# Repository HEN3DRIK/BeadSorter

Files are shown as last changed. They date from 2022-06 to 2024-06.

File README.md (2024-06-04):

- 👋 Hi, I’m @HEN3DRIK
- 👀 I’m interested in 3DPrinting and Electroforming/Electroplating
- 📫 How to reach me 
  - Youtube https://youtube.com/@hen3drik
  - Twitter https://twitter.com/hen3drik

# BeadSorter
Nice to have you here. In this repository I keep the files that are necessary for the BeadSorter. Also there will be documentation about the needed electronics and software. I will update this repo continuously.

# Video
perlerbead sorting machine (https://www.youtube.com/watch?v=CX-w85ZC5AQ)

# References
These are Projects necessary for this beadsorter to work.

Original Project by Linus Barth:
[BeadSort: Machine for sorting perler beads by LinusB - Thingiverse](https://www.thingiverse.com/thing:2598302)

Modified to skip aligner phase by RichA777
[Bead Sorter modified to skip aligner phase by RichA777 - Thingiverse](https://www.thingiverse.com/thing:4507571)
# Parts List
You'll need electronic parts for this bead sorter. This is alist of what i used in this project. I belive some components can be substituted.

- 1x Miniature-DC-Gear Motor 15RPM: https://www.amazon.de/gp/product/B08591W5N8/ref=ppx_yo_dt_b_asin_title_o08_s00?ie=UTF8&psc=1
- 2x LM2596S DC-DC: https://www.amazon.de/gp/product/B07YWLCTLK/ref=ppx_yo_dt_b_asin_title_o09_s00?ie=UTF8&psc=1
- 1x A4988 Stepper Driver Module: https://www.amazon.de/gp/product/B07C2V9GWC/ref=ppx_yo_dt_b_asin_title_o01_s00?ie=UTF8&psc=1
- 1x Nema 17 Stepper Bipolar 1A 16Ncm 42x20mm 4-Wires: https://www.amazon.de/dp/B06XVM38YW/ref=pe_27091401_487024491_TE_item
- 1x L298N Motor Drive Controller Board Module: https://www.amazon.de/gp/product/B07MY33PC9/ref=ppx_yo_dt_b_asin_title_o08_s01?ie=UTF8&psc=1
- 1x Adafruit-Sensor TCS34725 RGB: https://www.amazon.de/gp/product/B00OKCRU5M/ref=ppx_yo_dt_b_asin_title_o09_s01?ie=UTF8&psc=1
- 1x Arduino Nano V3.0 Atmega328 CH340: https://www.amazon.de/gp/product/B01MS7DUEM/ref=ppx_yo_dt_b_asin_title_o03_s00?ie=UTF8&psc=1
- 1x SG90 Micro Servo Motor 9G: [https://www.amazon.de/gp/product/B07CYZSVKW/ref=ppx_yo_dt_b_asin_title_o03_s00?ie=UTF8&psc=1](https://www.amazon.de/owootecc-Helicopter-Airplane-Remote-Controls/dp/B07RZK4K39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)
- 1x 100µF Capacitor
- 1x Resistor matching LED
- 1x White LED
- 1x Photo Resistor 5mm
- 1x Push Button
- Wires
- PTFE Spray

# Electronics Schema
I know, this isn't nice looking.
This whole thing is powered by a 12V power supply. I used a 9VA; That thing doesnt requiere a lot of current.
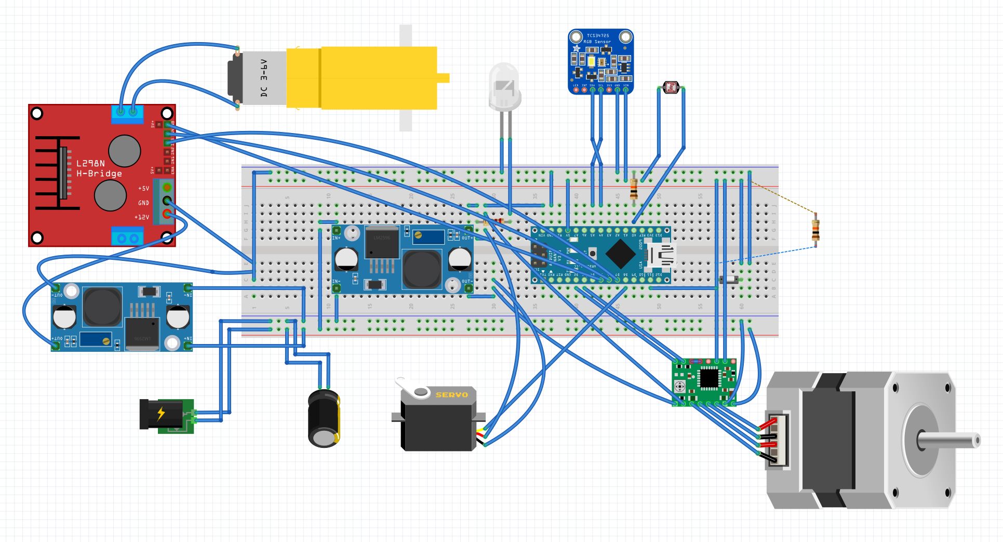
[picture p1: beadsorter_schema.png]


# Printing Guide
## Printing Linus Barth Parts
Print everything but the following Parts:
- 0-hopper-seq-plate.stl
- 0-hopper.stl
- 1-sequentializer-base.stl
- 1-sequentializer-ilc-corner.stl
- 1-sequentializer-tube-inset.stl
- 2-*.stl
- 3-analyzer-entry-tube.stl
- 4-dispatcher-tube-holder.stl
- 4-dispatcher-servo-holder.stl
- 4-dispatcher-base.stl
- 5-outputs-base.stl
- 5-outputs-slide-1.stl
- 5-outputs-slide-2.stl
- 5-outputs-slide-3.stl
- rpi-holder.stl

## Printing RichA777 parts
Print the following parts
- 0-hopper-seq-plate-4_holes_modified
- Sequencer_base_modified
- 0_Hopper_Modified_Cleaned_up

## Printing my parts
Print:
- 4x 1-sequentializer-ilc-corner_for_higher_motor.stl
- ring_container.stl
- 4_Stepper_shaft.stl
- Stepper_shaft_ring.stl
- Servo_base2.stl
- Stepper_shaft_ring.stl
- 3-analyzer-entry-tube_modified.stl
- UM2-Sequencer_tube_modified_tighter_Higher_Motor.stl
- 5-outputs-slide-1.stl
- 5-outputs-slide-2.stl
- 5-outputs-slide-3.stl
- holder_typeA.stl
- holder_typeB.stl
- Plate.stl
- Box_bottom.stl
- Box_lid.stl
- Box_top.stl

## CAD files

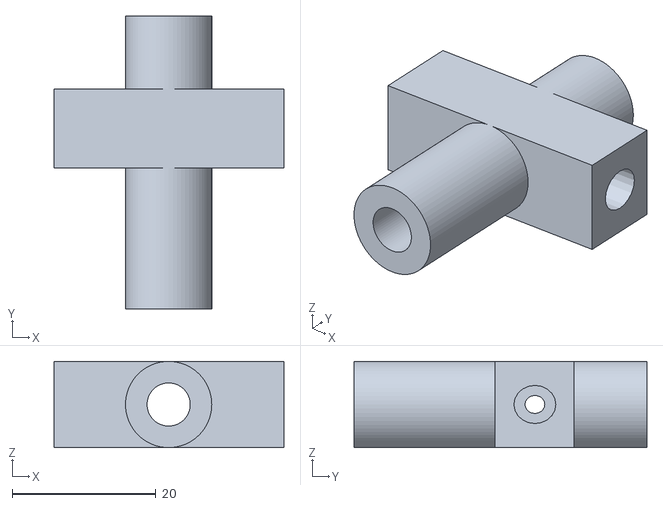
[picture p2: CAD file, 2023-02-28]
STLs/UM2_Sequencer_tube_modified_tighter_Higher_Motor.stl
32.0 x 40.7 x 12.0

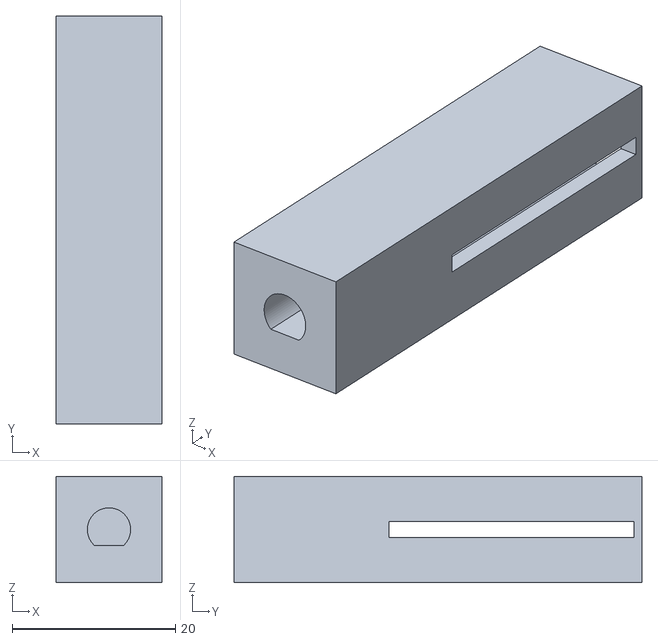
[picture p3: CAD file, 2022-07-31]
STLs/4_Stepper_shaft.stl
13.0 x 50.0 x 13.0

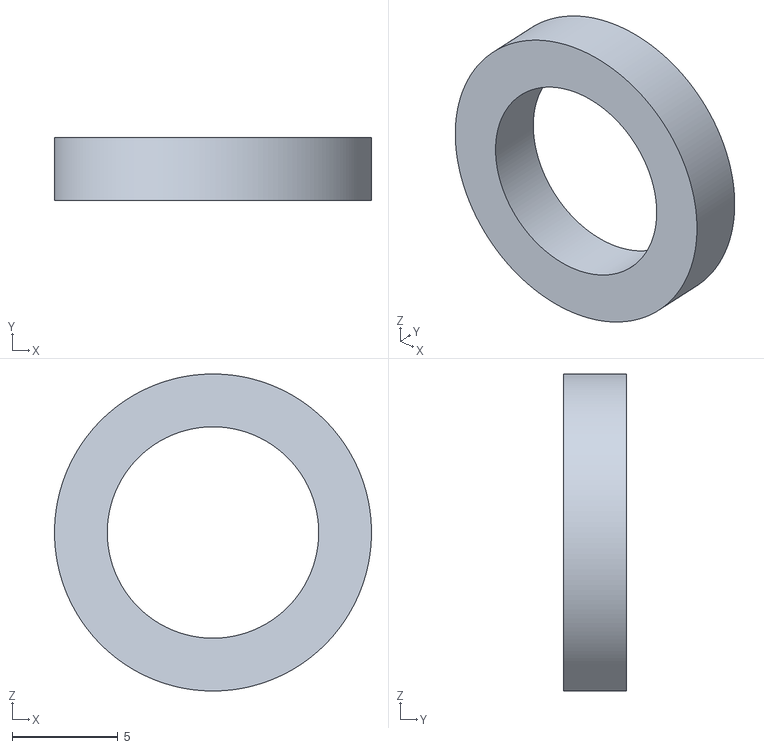
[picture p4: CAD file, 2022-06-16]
STLs/Stepper_shaft_ring.stl
15.0 x 3.00 x 15.0

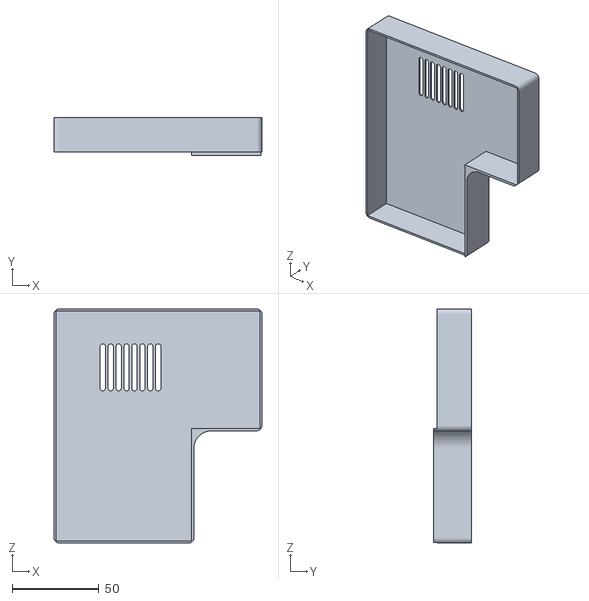
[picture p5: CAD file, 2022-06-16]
STLs/Box_top.stl
120.0 x 22.2 x 135.0

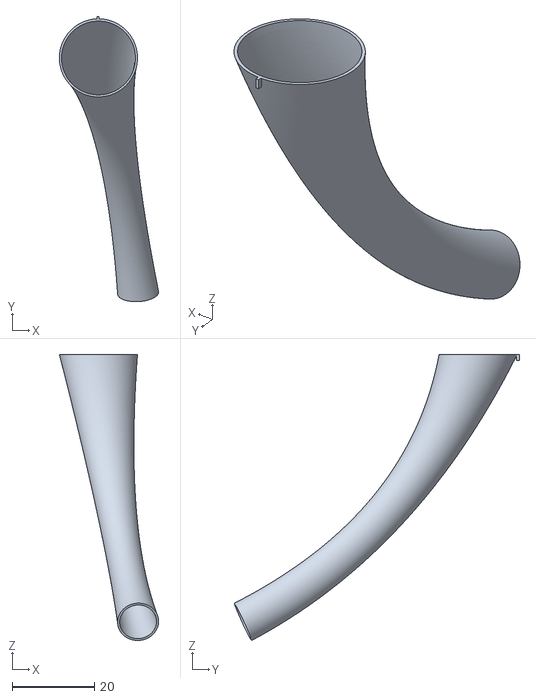
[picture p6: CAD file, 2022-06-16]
STLs/5-outputs-slide-2.stl
24.1 x 69.4 x 69.5

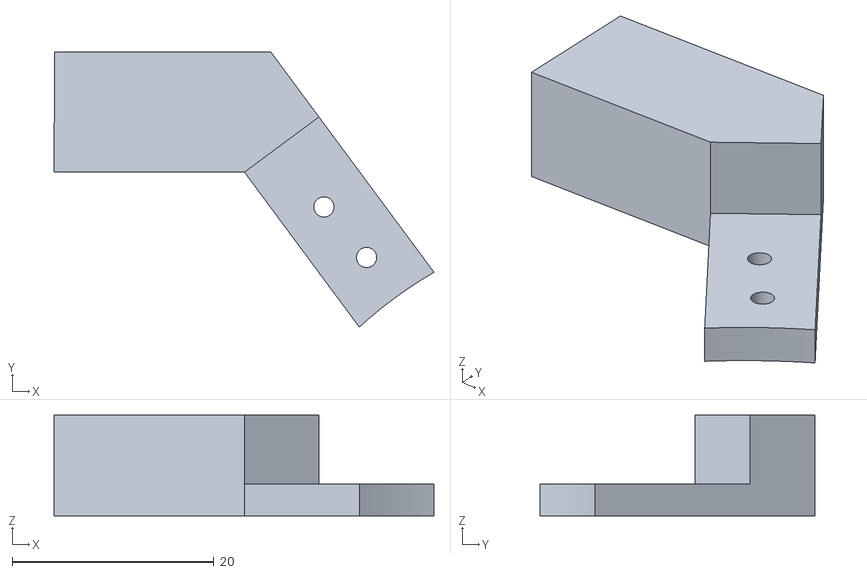
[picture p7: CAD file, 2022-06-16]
STLs/holder_typeA.stl
37.6 x 27.3 x 10.0

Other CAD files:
STLs/Decoration Fonts/Big/a_(Unsaved)_Body9_(Unsaved).stl
STLs/Decoration Fonts/Small/a.stl
STLs/Decoration Fonts/Big/a_(Unsaved)_Body7_(Unsaved).stl
STLs/Decoration Fonts/Small/d.stl
STLs/Decoration Fonts/Big/a_(Unsaved)_Body2_(Unsaved).stl
STLs/Decoration Fonts/Small/E_big.stl
STLs/Decoration Fonts/Big/a_(Unsaved)_Body3_(Unsaved).stl
STLs/Decoration Fonts/Small/T.stl
STLs/Decoration Fonts/Big/a_(Unsaved)_Body5_(Unsaved).stl
STLs/Decoration Fonts/Small/R.stl
STLs/Decoration Fonts/Big/a_(Unsaved)_Body4_(Unsaved).stl
STLs/Decoration Fonts/Small/O.stl
STLs/1-sequentializer-ilc-corner_for_higher_motor.stl
STLs/3-analyzer-entry-tube_modified.stl
STLs/5-outputs-slide-1.stl
STLs/5-outputs-slide-3.stl
STLs/Box_bottom.stl
STLs/Box_lid.stl
STLs/Decoration Fonts/Big/a_(Unsaved)_Body10_(Unsaved).stl
STLs/Decoration Fonts/Big/a_(Unsaved)_Body1_(Unsaved).stl
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

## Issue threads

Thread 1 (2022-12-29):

Missing STL-Files

Daffy2905, 2022-12-29:
Hi Hendrik,

I am missing some STL-Files, for example the files for the hopper ....
Greetings
David

Update: Sorry, i found the files in the STL-files form the other creators ....

Closed 2022-12-29.

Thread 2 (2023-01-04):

UM2_Sequencer_tube_modified_tighter_Higher_Motor.stl - seems to be wrong ....

Daffy2905, 2023-01-04:
Hi Hendrik!

It seems the noted file UM2_Sequencer_tube_modified_tighter_Higher_Motor.stl is not correct. I think the led and the photorisitor should have a connection, but in the file there is wall between them. Also the perlerbeads cannot fall down in the analyser because there is also a block.

THANK you for the great project ....
David

HEN3DRIK, 2023-02-28:
Thank you, sorry that it took so long. Fixed it.

Closed 2023-02-28.

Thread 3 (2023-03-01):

Probleme mit Servo in Bauelement 3

Fapi097, 2023-03-01:
Vorweg - beim Bau der Sorting machine, gab es weder elektrisch, noch drucktechnisch Probleme, außer bei Bauelement **"3-analyzer"**. Genauer gesagt liegt das Problem beim Servomotor, auf welchem **"3-analyzer-separation-arm"** befestigt ist und mit **"3-analyzer-exit-base"** sowie **"3-analyzer-exit-tube"** verbunden ist. Die Bügelperlen werden in diesem Abschnitt nicht richtig gefördert - das Problem liegt sowohl in der Aufnahme als auch Abgabe. Die Perlen scheinen sich im Übergang zwischen **seperation arm** und **analyzer exit tube** zu verfangen, obwohl ich alle mir erdenklichen Befestigungsmöglichkeiten und Servostellungen augeschöpft habe. (Zur besseren Darstellung habe ich eine Bilderstrecke sowie Videos über einen Dropboxlink zusammengefasst.) [https://www.dropbox.com/scl/fo/sogxwpxyg6pxwu0e42v44/h?dl=0&rlkey=3x28gm473k9n9inqbctwqn96i]
In der Software erschien mir die Möglichkeit der Änderung des Wertes in der Zeile _"#define angle 15 //Servo"_ nachvollziehbar, erzielte jedoch keine Wirkung.
Ich hoffe, dass Sie einen Lösungsweg für mein Problem haben, da ich sehr viel Spaß und Freude an diesem Projekt habe und es auch sehr gerne abschließen möchte.
Ich wünsche noch einen angenehmen Abend.
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

Mit freundlichen Grüßen

Fabian

HEN3DRIK, 2023-03-02:
Hi,

_Angle_ ist für die initiale Position des Arms (wird nur in der setup routine des code verwendet). Dieser muss so gewählt werden, dass er zu beginn bündig unter dem entry tube steht. Danach wird die funktion serveFeedOut() verwendet um die Bügelperle zum exit tube zu befördern. die werte 41,44,41,44,... verursachen ein wackeln, dass die perle hoffentlich herausbefördert. beim erneuten durchgang wird servoFeedIn() verwendet um unter dem entry tube ebenfalls etwas zu wackeln.

wie du sicherlich bemerkt hast dies der kniffeligste teil des sortierers. hier muss alles sehr glatt sein. es sind teilweise kleinste einstellungen, die dazuführen, dass die perle sich verheddert. ich erinnere mich wie lange ich an diesem mechanismus saß.

was du machen kannst:
- alles glatt schmirgeln, alle röhren, alle flächen. evtl. mit etwas PTFE spray abputze. auf deinen fotos sieht es so aus als hättest du das nicht gemacht. die röhren von innen richtig schön glatt feilen. zumindest die kurzen direkt am analyzer.
- die werte in servoFeedIn und servoFeedOut anpassen. deinen videos nach passen die nicht. du möchtest erreichen, dass der servo genau unter/über den röhren "wackelt".
-  ich hatte die teile auch erst grau gedruckt, danach habe ich alles im analyzer weiß gedruckt, was zu besserer erkennung führte.

ich weiß, ist richtig nervig. als ich es dann richtig eingestellt hatte lief es aber gut und macht seither keine probleme.

void servoFeedIn() {
  delay(200);
  servo.write(16);
  delay(200);
  servo.write(18);
  delay(200);
  servo.write(17);
  delay(200);
}

void servoFeedOut() {
  servo.write(41);
  delay(200);
  servo.write(44);
  delay(200);
  servo.write(41);
  delay(200);
  servo.write(44);
  delay(200);
  servo.write(41);
  delay(200);
  servo.write(44);
  delay(200);
  servo.write(41);
  delay(200);
  servo.write(44);
  delay(500);
}

Fapi097, 2023-03-02:
Danke das hilft mir schon sehr ich werde es probieren und mich melden wenn ich es geschaft habe.
Einen schönen Abend noch mit freundlichen grüße Fabian Schragner

Fapi097, 2023-03-03:
Danke für die hilfe mit dem Servo. Dieser Vorgang funktioniert einwandfrei. Leider hat sich ein anders Problem aufgetan Wenn ich die Maschine starte bewegt sich der stepper motor nicht und auch der farb scan auch nicht der servo bewegt sich 4 mal dannach stellt er seinen arbeit wieder ein nur mehr der  Hopper motor dreht das wars. Ich bin mir nicht ganz sicher ob der Stepper richtig am Driver verbunden ist .Und wieso die  maschine nicht automatisch zum sortieren anfang. vielen dank für ihre hilfe und ein Schönes Wochende noch mit freundlichen grüße Fabian

Daffy2905, 2023-03-09:
Bin auch gerade in der finalen Phase knapp vor Inbetriebnahme :-) Ich hatte ein änliches Problem mit der Analyzer und das die Perlen sich manchmal zwischen EntryTeil und Arm "verkeilen". Hab mich dann etwas mit dem Code vertraut gemacht und die von Hendrik erwähnten Werte adaptiert. Dies führte zu einer merklichen Verbesserung. Wie auch Hendrik geschrieben hat, alles muss glatt sein wie ein Babypopo. Die Toleranzen bewegen sich da im 0,irgendwas mm Bereich. Aber grundsätzlich bin ich absolut begeistert von dem Teil :-)

Fapi097, 2023-03-09:
ja Daffy2905 es ist ein wirklich cooles Projekt darf ich dir paar fragen stellen 1.wie hast du den Steppermotor angeschlossen 2. bei mir sortiert die Maschine nicht im autostart und wie bekomme ich die farben konfiguriert. besten dank und einen schönen abend noch

Daffy2905, 2023-03-09:
1. Wie am Schema dargstellt, funktioniert soweit
2. Ich würde mal ein USB-Kabel an Arduino während dem Betrieb anschließen und mit dem Serial Monitor der Arduino Software mitschauen, was das Teil macht. Da bekommst im Log mit, was nicht passt .....
LG

Fapi097, 2023-03-12:
im log steht zwar color reading aber es passiert nichts haha

Fapi097, 2023-03-12:
soll ich mal den Log posten

Fapi097, 2023-03-12:
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

Daffy2905, 2023-03-13:
Passiert überhaupt nichts? Also beim Start sollte der ServoMotor im Analyzer 6 Mal hin- und her fahren, es wird die initiale Farbkalibrierung durchgeführt. Anschließend sollte der HopperMotor starten und der Spaß beginnt. Spannungen alle überprüft? Die Verkabelung ist im ersten Moment etwas tricky, aber nach längerer Beschäftigung wird vieles schnell klar ...

Fapi097, 2023-03-13:
ja das macht er auch aber dannach passiert nichts mehr also er fährt 6 mal hin und her de hopper motor fördert aber das wars der servo arm bleid dann einfach stehen mit einer Bügelperle drinnen und das wars

HEN3DRIK, 2023-03-14:
Es liegt vermutlich an dieser Stelle in Zeile 123..125

```
if (digitalRead(setupPin) == HIGH) {
  while (digitalRead(setupPin) == HIGH) {
  }
```

Wenn der Taster gedrückt ist schaltet das Gerät in den manuellen Modus. Überprüf mal die Verkabelung oder kommentier diese Bedingung testweise aus (123-131)

Fapi097, 2023-03-14:
Oky ich probiere es mal Danke schön Tag noch

Fapi097, 2023-03-15:
Es tut mir wirklich leid das ich so nerv tötend bin mit meinen Fragen. Ich habe die Verkabelung anders umgesetzt und ich weiß nicht ob das zu 100 % richtig ist.

Fapi097, 2023-03-15:
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
Ist der Schaltplan so richtig.

Daffy2905, 2023-03-15:
Wieviel Volt gibt der Nano dann aufs BreakoutBoard aus? Wennst nur mit 5V in den Nano reingehst kommen am V+-Ausgang ned mehr als 4V raus für die anderen Komponenten wie der FarbSensor ....Von meinem/meiner Galaxy gesendet
-------- Ursprüngliche Nachricht --------Von: Fapi097 ***@***.***> Datum: 15.03.23  20:41  (GMT+01:00) An: HEN3DRIK/BeadSorter ***@***.***> Cc: Daffy2905 ***@***.***>, Comment ***@***.***> Betreff: Re: [HEN3DRIK/BeadSorter] Probleme mit Servo in Bauelement 3 (Issue #3)

Ist der Schaltplan so richtig.

—Reply to this email directly, view it on GitHub, or unsubscribe.You are receiving this because you commented.Message ID: ***@***.***>

Daffy2905, 2023-03-15:
Und Dir fehlen beim StepperModul die 12V ...Von meinem/meiner Galaxy gesendet
-------- Ursprüngliche Nachricht --------Von: Fapi097 ***@***.***> Datum: 15.03.23  20:41  (GMT+01:00) An: HEN3DRIK/BeadSorter ***@***.***> Cc: Daffy2905 ***@***.***>, Comment ***@***.***> Betreff: Re: [HEN3DRIK/BeadSorter] Probleme mit Servo in Bauelement 3 (Issue #3)

Ist der Schaltplan so richtig.
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
Fapi097, 2023-03-16:
Danke für die hilfe ich werde das mal überprüfen

Fapi097, 2023-03-19:
habe alles nochmal nachgebaut jetzt sortiert er Automatisch aber der knopf funkoniert nicht also das mit die vier farben wie gehört der taster richtig angeschlossen . Aber er sagt immer color not found auser 2 farben gelb und blau
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

Daffy2905, 2023-03-19:
Ich kämpfe ständig mit der Zuverlässigkeit des Förderungsprozesses. Mal bleiben die Perlen beim Eingang Analyzer hängen, dann verkeilen sie sich zwischen Arm und Eingang Analyzer oder bleiben unten im Verteilerarm drinnen hängen. Hab schon alles geschliffen, PTFE-Spray drauf, aber so schön flüssig wie im Video von HENDRIK läufts leider bei mir - und leider steigt auch schon langsam der Frustrationsgrad, obwohl ich vom Projekt echt echt begeistert bin .....

Fapi097, 2023-03-19:
Ja Kenn ich gut ich habe das gelöst mit den einstellen im adruino code  mit denn werten einstellen das funktioniert super
Aber ich hab mit der Dispatcher problem also das er richtig dreht und die farbe erkennt ich verstehe das nicht ganz wie das geht bei mir steht nur immer new container haha ja bei mir  steigt leider auch immer mehr die Frustration aber vieleicht können wir uns gegenseitig helfen.

HEN3DRIK, 2023-03-19:
Ich kann euch gut verstehen. Bei dem Projekt braucht man starke Nerven. Auch ich startete sehr euphorisch und am ende habe ich dann die software neugeschrieben und zig Teile verändert, dass es überhaupt mal lief. Was ich sagen will, es zahlt sich mehr oder weniger aus. Wenn das Ding dann mal 2000 Perlen durchsortiert hat freut man sich schon sehr. In der ganzen Zeit hätte man es aber auf per Hand sortieren können, aber das ist ja nicht die Motivation 😅. Ich habe ihn letzten auch noch einmal angeworfen um nachzugucken wie etwas genau funktioniere und dann habe ich ihn mal laufen lassen lassen: klappt immer noch gut. Sorry, dass ich so selten dazu komme zu antworten:

Zu den Problemen:
@Daffy2905 ich hatte oft deformierte Perler drin, die verstopfen alles. Ansonsten macht es sinn das Röhrchen über dem Analyzer und das exit Röhrchen mit gröberen schleifpapier in eine richtung zu weiten (wie so rillen = wenig kontaktfläche) und dann ptfe dran. aber das ptfe sparsam und "polieren". Im Verteilerarm: Wo genau? bei mir manchmal in den organischen Röhren. Keine Ahnung wie sich das verkeilt, ist wohl alles eine Frage den Anzahl an Perlen.

@Fapi097 Der Sorter hat eine Kapazität von 11 Plätzen für Farben und eine Learning/NichtErkannt Platz. Wenn der Sorter im AutoSort ist (Knopf nicht gedrückt) lernt er die Farbe, wenn er sie nicht kennt an und wirft sie sofort wieder aus (not found + not allContainerFull -> StoreColor). Wir diese Farbe nun das NÄCHSTE mal erkannt, fährt der dispatcher auf die vorher gespeicherte Position. Es ist wichtig zu verstehen, dass der Sorter die Farben lernt/speichert (max 16 stück in tempStoredColors) und diese in dynamicContainerArray (max 11) zuordnet (je nachdem welche zuerst kommt).

Viel Glück und Durchhaltekraft!

Fapi097, 2023-03-20:
Danke das hat mir sehr viel geholfen also einfach mal sortieren lassen eine zeitlang habe den Vorgang immer abgebrochen weil ich die Meldung in Serial Monitor gesehn haben. Und für was ist dann der Modus mit dem Knopf.
Ich werde das Projekt sicher bis zum Schluss durchhalten ich danke dir wirklich für deine Hilfe.

Fapi097, 2023-03-24:
Guten Morgen @Daffy2905 bei mir Funktioniert jetzt alles fast reibungslos nur die Drehscheibe vom Hopper ist ein Problem weil die Perlen nicht durch fallen und sich verkeilen zwischen Scheibe und Hopperauslass. Welchen Motor benutzt und wie schnell dreht der.

Daffy2905, 2023-03-24:
Freut mich - also die Geschwindigkeit des Hoppermotors (hab den DC6V 30RPM) kannst Du entweder über die Spannung regeln, hab glaub ich bei mir 7V als auch über die Zeile 11 (#define motorSpeed 255 //Container Motor) - stell hier mal einen Wert von unter 100 ein, da solltest schon eine Drehgeschwindigkeitsreduktion sehen .....

Fapi097, 2023-03-24:
@Daffy2905 ja das hab ich schon alles ausgetestet aber die Perlen werden immer eingeklemmt zwischen Drehscheibe und Dem Loch habe aber alles geschliffen und ausgerichtet aber die Bleiben immer stecken.

Fapi097, 2023-03-24:
@Daffy2905 habe auf 150 eingestellt hat aber nichts gebracht es kommt immer so raus wie auf den foto das es sich verkeilt.
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

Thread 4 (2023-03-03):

Danke für die hilfe mit dem Servo. Dieser Vorgang funktioniert einwandfrei. Leider hat sich ein anders Problem aufgetan Wenn ich die Maschine starte bewegt sich der stepper motor nicht und auch der farb scan auch nicht der servo bewegt sich 4 mal dannach stellt er seinen arbeit wieder ein nur mehr der  Hopper motor dreht das wars. Ich bin mir nicht ganz sicher ob der Stepper richtig am Driver verbunden ist .Und wieso die  maschine nicht automatisch zum sortieren anfang. vielen dank für ihre hilfe und ein Schönes Wochende noch mit freundlichen grüße Fabian

Fapi097, 2023-03-03:
Danke für die hilfe mit dem Servo. Dieser Vorgang funktioniert einwandfrei. Leider hat sich ein anders Problem aufgetan Wenn ich die Maschine starte bewegt sich der stepper motor nicht und auch der farb scan auch nicht der servo bewegt sich 4 mal dannach stellt er seinen arbeit wieder ein nur mehr der  Hopper motor dreht das wars. Ich bin mir nicht ganz sicher ob der Stepper richtig am Driver verbunden ist .Und wieso die  maschine nicht automatisch zum sortieren anfang. vielen dank für ihre hilfe und ein Schönes Wochende noch mit freundlichen grüße Fabian

_Originally posted by @Fapi097 in https://github.com/HEN3DRIK/BeadSorter/issues/3#issuecomment-1454113488_

HEN3DRIK, 2023-03-14:
I closed this: Copy of https://github.com/HEN3DRIK/BeadSorter/issues/3#issuecomment-1454113488

Closed 2023-03-14.

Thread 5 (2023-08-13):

Parts list incomplete and 1 broken link

Columbo, 2023-08-13:
May I ask you to add some amazon links for the following parts?:
1x 100µF Capacitor
1x Resistor matching LED
1x White LED
1x Photo Resistor 5mm
1x Push Button

The link for SG90 Micro Servo Motor 9G does not work anymore.

Some additional questions:
Which breadboard startet kit could you recommend?
What kind of resistors did you use? Could you add an amazon link for them?
Which power supply did you use? How many Volt and how many Ampere are necessary?

Would a starter kit like the following example be enough?
https://www.amazon.de/dp/B09ZX4CYDT/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

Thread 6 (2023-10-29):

Attaching tubes to plate

konforce, 2023-10-29:
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

I've got most of the project assembled, but am not understanding how the tubes are supposed to attach. Is the intention that the tabs of the tubes are supposed to fit in the corresponding slots in the rings?

On the plates.stl file, only three of the rings have slot cut out. (On the attached image, it is the three nearest ones.) Is this an incomplete STL or am I misunderstanding?

Also, did you glue the tubes or just friction fit?

HEN3DRIK, 2023-10-29:
Hi, i think i tried adding some alignement slots, but it's just super glueing them onto the ring. 😉

konforce, 2023-10-30:
There's three different versions of the slides - is the intention to print out four of each?

HEN3DRIK, 2024-08-16:
yes

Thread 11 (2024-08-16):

Consolidate STL files?

pdgonzalez872, 2024-08-16:
Hi @HEN3DRIK , amazing work.

I have a question:

I'm assuming why the reason you are not consolidating all the files that need to be printed is to give credit where its due to the folks in thingyverse. Is that correct? If so, awesome.

If not (and you find a different way to give credit and attribution -maybe tag the OG folks or name the files accordingly), do you think it's a good idea to put them all under the same folder?

Thanks!

bibz0r, 2025-01-06:
Is probably a good idea, I had to make a Excel file to keep track of which files to print and which not.

License-wise it should be possible too:

Remix by RichA777 is licensed under the Creative Commons - Attribution license.
BeadSort: Machine for sorting perler beads by LinusB is licensed under the Creative Commons - Attribution - Share Alike license

When I'm finished I'll probably submit a PR or fork it entirely, I'm not sure yet. I guess @HEN3DRIK is busy enough with other stuff anyways.

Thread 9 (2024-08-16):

Micro stepping configuration

iliar-rabet, 2024-08-16:
Hello,

Thanks for sharing this. I have set up everything but the machine is not very accurate. On the A4988, I have used the following set up for micro stepping:
MS1 : H
MS2: H
MS3: L
This would give me a step resolution of 1/8 of the full. Is this what you have used?

Second question: some times the stepper motor stops at some locations that are blocked and there is no container.
Do we have to manually spin the tube so it is initialized at some specific point?

Bests,
Iliar

HEN3DRIK, 2024-08-16:
Hi,

i connected to MS2 + MS1.
then I set #define stepperMulti 100 //Stepper

This gave me a very fine resolution.
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

The stepper needs to be in a certain position
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

iliar-rabet, 2024-08-16:
OK, thanks so much.
It is kind of hard to be sure which tube is the initial position by looking at this picture.
Is it tube number 5 if we count anti-clockwise starting from the stepper?

HEN3DRIK, 2024-08-16:
It actually doesent matter. The stepper moves clockwise and ist okay to start on the 3rd tube of each quarter. the 2nd (in this case the left next to picture position) is the last tube of the array (12th) so it will move there first after scanning a new bead. When the scanned bead is recognized after that it'll be sorted in 1 (position on the picture) 2,3 and so on. It wil skip the beam between pos 1 and 2 automatically.

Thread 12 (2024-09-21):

step files

3dfixer, 2024-09-21:
not really an issue
any chance of having the stl files as step files
i'm looking into making an airgun pellet weighing machine and would like to use your idea as a base to start from.
some of the stl's dont want to convert from stl to a form i can model from

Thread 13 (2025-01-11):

Missing stl file for aligner

Columbo, 2025-01-11:
I built the bead sorter but I have some issues with the the analyzer. Without the aligner the beads often get stuck between the sequentializer and the analyzer.

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

I guess that the exit from the sequentializer is not exactly in the middle of the entry of the analyzer.

Therefore I tried to use the aligner, printed all parts and tested the aligner without a motor by moving it manually a little bit with my fingers. Everything worked like a charm. Then I bought a motor for the aligner and I am wondering how the motor moves the aligner. It seems that you printed the whole aligner and one part that the motor of the aligner is connected to. But neither in your repo nor in the stl files of Linus seems to be this part.

May I ask you to add this part to your repo and some information how the aligner is moved by powering the motor? It would be nice if you could help me with the experiences you made with the aligner.

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

Columbo, 2025-01-13:
I just added some weight by printing a piece similar to a vibration motor and connected it to the end of my motor. Now it works and I am doing some testing with different weights:

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
[2-aligner-vibration-motor-ending.zip](https://github.com/user-attachments/files/18393108/2-aligner-vibration-motor-ending.zip)

Closed 2025-01-13.

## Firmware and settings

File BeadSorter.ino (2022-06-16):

#include <Servo.h>
#include <AccelStepper.h>
#include <Wire.h>
#include <Adafruit_TCS34725.h>

#define dirPin 2 //Stepper
#define stepPin 3 //Stepper
#define motorInterfaceType 1 //Stepper
#define stepperMulti 100 //Stepper

#define motorSpeed 255 //Container Motor
#define GSM2 5 // Container Motor
#define in3 7 //Container Motor
#define in4 6 //Container Motor

#define setupPin 11 //Setup
#define photoSensorPin A0 //Photo Sensor
#define nullScanOffset 200 

#define angle 15 //Servo

// Parameters: https://learn.adafruit.com/adafruit-color-sensors/program-it
//Adafruit_TCS34725 tcs = Adafruit_TCS34725(TCS34725_INTEGRATIONTIME_24MS, TCS34725_GAIN_1X);
Adafruit_TCS34725 tcs = Adafruit_TCS34725(TCS34725_INTEGRATIONTIME_50MS, TCS34725_GAIN_1X);
//Adafruit_TCS34725 tcs = Adafruit_TCS34725(TCS34725_INTEGRATIONTIME_101MS, TCS34725_GAIN_1X);

//Max allowed color difference = thresholdFactor ∗ colorValue + offset (0,08/40)
//dark colors 0.02 + 10
float thresholdFactor = 0.04;
int offset = 40;

Servo servo;
AccelStepper stepper = AccelStepper(motorInterfaceType, stepPin, dirPin);

boolean autoSort = true;
int errorCounter = 0;
int maxErrorCounter = 2;
int resultColor[4] = {0, 0, 0, 0};
int medianColors[4][4];
int storedColors[16][4];
int tempStoredColors[16][4];

int photoSensor = 0;

boolean calibrateNullScan = true;
int nullScanValues[4] = {6618, 1860, 2282, 2116}; //adjust these if no calibration

int autoColorCounter = 0;
int beadCounter = 0;

const int dynamicContainerArraySize = 16;
int dynamicContainerArray[dynamicContainerArraySize] = { -1, 666, -1, -1, -1, 666, -1, -1, -1, 666, -1, -1, -1, 666 , -1 , -1};

void setup() {
  pinMode(GSM2, OUTPUT);
  pinMode(in3, OUTPUT);
  pinMode(in4, OUTPUT);

  pinMode(setupPin, INPUT);
  //  pinMode(stepperTunerPin, INPUT);

  Serial.begin(9600);
  Serial.println("");
  Serial.println("BeadSorter start");

  //Serial.println("Analyzer start");
  servo.attach(8);
  servo.write(angle);

  //stepper.setMaxSpeed(4000);
  //stepper.setAcceleration(5000);
  stepper.setMaxSpeed(6000);
  stepper.setAcceleration(9000);
  stepper.setCurrentPosition(0);

  if (tcs.begin()) {
    Serial.println("Sensor found");
  } else {
    Serial.println("TCS34725 not found ... exiting!");
    while (1); // Stop program
  }

  if (!autoSort) {
    Serial.println("Import default Colors");
    importDefaultColorSet();
  }

  if (calibrateNullScan) {
    Serial.print("Calibrating: ");
    for (int i = 0; i < 6; i++) {
      Serial.print(i);
      servoFeedIn();
      servoFeedOut();
    }
    Serial.println("");
    servoFeedIn();
    readColorSensor();
    setNullScanValues();
  }

  Serial.println("Starting continous color scan.");
  Serial.println("");
}

void loop() {
  photoSensor = analogRead(photoSensorPin);
  //Serial.println("");Serial.println(photoSensor);

  if (photoSensor > 750) {
    if (!digitalRead(in3) && !digitalRead(in4)) {
      digitalWrite(in3, LOW);  // start
      digitalWrite(in4, HIGH);
      analogWrite(GSM2, motorSpeed);
    }
    //Serial.println("Photosensor OK");
  } else {
    digitalWrite(in3, LOW);  // stop
    digitalWrite(in4, LOW);
    Serial.println("Photosensor Fail");
    //analogWrite(GSM2, 0);
  }

  if (digitalRead(setupPin) == HIGH) {
    while (digitalRead(setupPin) == HIGH) {
    }
    // for manual colors, there are more restricted thresholds
    autoSort = false;
    thresholdFactor = 0.03;
    offset = 20;
    addColor();
  }

  //  if (digitalRead(stepperTunerPin) == HIGH) {
  //    while (digitalRead(stepperTunerPin) == HIGH) {
  //    }
  //    moveStepperForward();
  //  }

  servoFeedIn();
  readColorSensor();

  if (!nullScan()) {
    Serial.println("");
    Serial.print("Beads analyzed: "); Serial.println(beadCounter++);
    Serial.print("\tClear:"); Serial.print(resultColor[0]);
    Serial.print("\tRed:"); Serial.print(resultColor[1]);
    Serial.print("\tGreen:"); Serial.print(resultColor[2]);
    Serial.print("\tBlue:"); Serial.print(resultColor[3]);
    Serial.println("");
    sortBeadToDynamicArray();
    errorCounter = 0;
  } else {
    Serial.print(".");
    errorCounter++;
  }

  servoFeedOut();

  //Serial.print("errorcounter: ");Serial.print(errorCounter);Serial.print(" maxErrorCounter:"); Serial.println(maxErrorCounter);
  if (errorCounter >= maxErrorCounter) {
    reverseContainerMotor();
    errorCounter = 0;
  }

}

void addColor() {
  int colorIndex;

  clearMedianColors();
  stopMotor();

  Serial.print("Insert Color to register. Press button when done...");

  while (digitalRead(setupPin) == LOW) {
  }

  startMotor();
  delay(10000);
  stopMotor();
  for (int i = 0; i < 4; i++) {
    Serial.print(i + 1); Serial.print("/4: ");
    servoFeedIn();
    readColorSensor();

    addColorToMedianColors(i);

    servoFeedOut();
  }

  calcMedianAndStore();
  startMotor();
}

void servoFeedIn() {
  delay(200);
  servo.write(16);
  delay(200);
  servo.write(18);
  delay(200);
  servo.write(17);
  delay(200);
}

void servoFeedOut() {
  servo.write(41);
  delay(200);
  servo.write(44);
  delay(200);
  servo.write(41);
  delay(200);
  servo.write(44);
  delay(200);
  servo.write(41);
  delay(200);
  servo.write(44);
  delay(200);
  servo.write(41);
  delay(200);
  servo.write(44);
  delay(500);
}

void readColorSensor() {
  
  // Sensor returns R G B and Clear value
  uint16_t clearcol, red, green, blue;
  delay(200); // Farbmessung dauert c. 50ms
  tcs.getRawData(&red, &green, &blue, &clearcol);

  resultColor[0] = clearcol;
  resultColor[1] = red;
  resultColor[2] = green;
  resultColor[3] = blue;
}

int addColorToMedianColors(int noOfTest) {
  medianColors[ noOfTest ][ 0 ] += resultColor[0];
  medianColors[ noOfTest ][ 1 ] += resultColor[1];
  medianColors[ noOfTest ][ 2 ] += resultColor[2];
  medianColors[ noOfTest ][ 3 ] += resultColor[3];
}

int getNextFreeArrayPlace() {
  int arrayCounter = 0;
  while (
    (storedColors[ arrayCounter ][ 0 ] > 0) and
    (storedColors[ arrayCounter ][ 1 ] > 0) and
    (storedColors[ arrayCounter ][ 2 ] > 0) and
    (storedColors[ arrayCounter ][ 3 ] > 0)) {
    arrayCounter++;
  }
  return arrayCounter;
}

void clearMedianColors() {
  memset(medianColors, 0, sizeof(medianColors));
}

void calcMedianAndStore() {
  memset(resultColor, 0, sizeof(resultColor));
  for (int i = 0; i < 4; i++) {
    for (int j = 0; j < 4; j++) {
      resultColor[i] += medianColors[ j ][ i ];
    }
    resultColor[i] = resultColor[i] / 4;
  }

  int nextColorNo = getNextFreeArrayPlace();

  for (int i = 0; i < 4; i++) {
    storedColors[ nextColorNo ][ i ] = resultColor[i];
  }

  Serial.print("I stored color to bank #"); Serial.print(nextColorNo);
  Serial.println("");
}

void importDefaultColorSet() {
  storeColor(0, 1032, 854, 766); //Orange
  storeColor(1, 1331, 1321, 918); //Bright Yellow
  storeColor(2, 532, 914, 797); //Green
  storeColor(3, 512, 845, 967); //Dark Blue
  storeColor(4, 1257, 1151, 1129); //Rose
  storeColor(5, 1265, 1215, 1100); //Skin
  storeColor(6, 756, 757, 721); // Red
  storeColor(7, 1525, 1858, 1735); //White
  storeColor(8, 512, 742, 700); //Black
  storeColor(9, 939, 1462, 1101); //Lime Green
  storeColor(10, 712, 1298, 1121); //Mint Green
  storeColor(11, 1213, 975, 914); //Coral
  storeColor(12, 1185, 1115, 876); //Dark Yellow
}

String getColorNameFromNo(int colorNo) {
  switch (colorNo) {
    case 0: return "Orange";
    case 1: return "Bright Yellow";
    case 2: return "Green";
    case 3: return "Dark Blue";
    case 4: return "Rose";
    case 5: return "Skin";
    case 6: return "Red";
    case 7: return "White";
    case 8: return "Black";
    case 9: return "Lime Green";
    case 10: return "Mint Green";
    case 11: return "Coral";
    case 12: return "Dark Yellow";
    default: return "Unknown";
  }
}

void storeColor(int index, int red, int green, int blue) {
  storedColors[ index ][0] = index;
  storedColors[ index ][1] = red;
  storedColors[ index ][2] = green;
  storedColors[ index ][3] = blue;
  //  storedColors[ index ][4] = 1;
}

boolean nullScan() {
  if ((resultColor[0] > (nullScanValues[0] - nullScanOffset) and resultColor[0] < (nullScanValues[0] + nullScanOffset)) and
      (resultColor[1] > (nullScanValues[1] - nullScanOffset) and resultColor[1] < (nullScanValues[1] + nullScanOffset)) and
      (resultColor[2] > (nullScanValues[2] - nullScanOffset) and resultColor[2] < (nullScanValues[2] + nullScanOffset)) and
      (resultColor[3] > (nullScanValues[3] - nullScanOffset) and resultColor[3] < (nullScanValues[3] + nullScanOffset))) {
    return true;
  }
  return false;
}

void setNullScanValues() {
  nullScanValues[0] = resultColor[0];
  nullScanValues[1] = resultColor[1];
  nullScanValues[2] = resultColor[2];
  nullScanValues[3] = resultColor[3];

  Serial.print("Calibration results: "); Serial.print(nullScanValues[0]); Serial.print(" "); Serial.print(nullScanValues[1]); Serial.print(" "); Serial.print(nullScanValues[2]); Serial.print(" "); Serial.print(nullScanValues[3]); Serial.println("");
}

void sortBeadToDynamicArray() {
  int threshold;
  int upperLimit;
  int lowerLimit;
  boolean found =  false;

  copyColorsToTemp();

  Serial.println("Analyzing Results:");

  for (int i = 0; i < 16; i++) {
    threshold = thresholdFactor * resultColor[1] + offset;
    upperLimit = resultColor[1] + threshold;
    lowerLimit = resultColor[1] - threshold;
    //        Serial.print(i);Serial.print(":R:"); Serial.print(threshold);Serial.println("");
    //        Serial.print(i);Serial.print(":R:"); Serial.print(upperLimit);Serial.println("");
    //        Serial.print(i);Serial.print(":R:"); Serial.print(lowerLimit);Serial.println("");
    //        Serial.println(tempStoredColors[ i][1]);
    if (tempStoredColors[ i ][1] >= lowerLimit and tempStoredColors[ i ][1] <= upperLimit) {
      threshold = thresholdFactor * resultColor[2] + offset;
      upperLimit = resultColor[2] + threshold;
      lowerLimit = resultColor[2] - threshold;
      //
      //            Serial.print(i);Serial.print(":G:"); Serial.print(threshold);Serial.println("");
      //            Serial.print(i);Serial.print(":G:"); Serial.print(upperLimit);Serial.println("");
      //            Serial.print(i);Serial.print(":G:"); Serial.print(lowerLimit);Serial.println("");

      if (tempStoredColors[ i ][2] >= lowerLimit and tempStoredColors[ i ][2] <= upperLimit) {
        threshold = thresholdFactor * resultColor[3] + offset;
        upperLimit = resultColor[3] + threshold;
        lowerLimit = resultColor[3] - threshold;
        //
        //                Serial.print(i);Serial.print(":B:"); Serial.print(threshold);Serial.println("");
        //                Serial.print(i);Serial.print(":B:"); Serial.print(upperLimit);Serial.println("");
        //                Serial.print(i);Serial.print(":B:"); Serial.print(lowerLimit);Serial.println("");

        if (tempStoredColors[ i ][3] >= lowerLimit and tempStoredColors[ i ][3] <= upperLimit) {
          //          Serial.print("Color is #"); Serial.print(tempStoredColors[ i ][0]); Serial.println("");
          if (autoSort) {
            Serial.print("Color is R:"); Serial.print(tempStoredColors[ i ][1]); Serial.print(" G:"); Serial.print(tempStoredColors[ i ][2]); Serial.print(" B:"); Serial.print(tempStoredColors[ i ][3]);
            //            updateStoredColorCount(i);
            //            updateDetectedColorFromTempStoredColor(i);
          } else {
            Serial.print("Color is #"); Serial.print(getColorNameFromNo(tempStoredColors[ i ][0])); Serial.print(". ");
          }
          //Serial.println(tempStoredColors[ i ][0]);

          int containerNo = getContainerNo(tempStoredColors[ i ][0]);
          //Serial.print("move stepper to container No:"); Serial.println(containerNo);
          moveSorterToPosition(containerNo);
          found = true;
          break;
        }
      }
    }
  }

  if (!found) {
    Serial.println("not found");
    if (autoSort) {
      Serial.println("autosort!");
      if (!allContainerFull()) {
        Serial.println("not allContainerFull. StoreColor");
        storeColor(autoColorCounter, resultColor[1], resultColor[2], resultColor[3]);
        autoColorCounter++;
        moveSorterToPosition(dynamicContainerArraySize - 1);
      } else {
        moveSorterToPosition(dynamicContainerArraySize - 1);
      }
    } else {
      moveSorterToPosition(dynamicContainerArraySize - 1);
    }
  }
}

int getContainerNo(int colorIndex) {
  int containerNo = -1;
  int i = 0;

  for (i; i < dynamicContainerArraySize; i++) {
    //Serial.print("looking for ");Serial.print(colorIndex);Serial.print(" at position ");Serial.println(i);
    if (colorIndex == dynamicContainerArray[i]) {
      Serial.print("Color found in container array: "); Serial.println(dynamicContainerArray[i]);
      containerNo = i;
      break;
    }
  }

  if (containerNo == -1) {
    if (allContainerFull()) {
      containerNo = 15;
    } else {
      containerNo = getNextContainerNo(colorIndex);
    }
  }

  return containerNo;
}

int getNextContainerNo(int colorIndex) {
  Serial.println("finding container for new color");
  int arrayCounter = 0;

  while ((dynamicContainerArray[ arrayCounter ] > -1)) {
    arrayCounter++;
  }
  dynamicContainerArray[arrayCounter] = colorIndex;

  Serial.print("Return Color Index: "); Serial.print(colorIndex); Serial.println("");
  return arrayCounter;
}

bool allContainerFull() {
  int arrayCounter = 0;
  //Serial.println("testing all container full");

  while ((dynamicContainerArray[ arrayCounter ] > -1)) {
    arrayCounter++;
  }

  return arrayCounter >= 15;
}

void copyColorsToTemp() {
  memcpy(tempStoredColors, storedColors, sizeof(tempStoredColors));
}

void moveSorterToPosition(int position) {
  int currentPos = stepper.currentPosition() / stepperMulti;
  int diffToPosition = abs(position - currentPos);

  // TODO: Es wird nur sequentiell angesteuert. 
  //  if ((diffToPosition)>8){
  //    int diff = 16 - diffToPosition ;
  //    position = -diff;
  //  }

  position *= stepperMulti;

  stepper.moveTo(position);
  stepper.runToPosition();
}

void stopMotor() {
  digitalWrite(in3, LOW);
  digitalWrite(in4, LOW);
  analogWrite(GSM2, motorSpeed);
}

void startMotor() {
  digitalWrite(in3, HIGH);
  digitalWrite(in4, LOW);
  analogWrite(GSM2, motorSpeed);
}

void reverseContainerMotor() {

  if (digitalRead(in3)) {
    digitalWrite(in3, LOW);
  } else {
    digitalWrite(in3, HIGH);
  }

  if (!digitalRead(in4)) {
    digitalWrite(in4, HIGH);
  } else {
    digitalWrite(in4, LOW);
  }

  analogWrite(GSM2, motorSpeed);
}

//void updateDetectedColorFromTempStoredColor(int i) {
//  Serial.println(""); Serial.println("Updating color.");
//  Serial.println(""); Serial.print("Red before: "); Serial.print(storedColors[ i ][1]); Serial.print(" Color Counter: "); Serial.print(storedColors[ i ][4]);
//  storedColors[ i ][1] = ((storedColors[ i ][1] * (storedColors[ i ][4] - 1)) + (resultColor[1])) / storedColors[ i ][4];
//  storedColors[ i ][2] = ((storedColors[ i ][2] * (storedColors[ i ][4] - 1)) + (resultColor[2])) / storedColors[ i ][4];
//  storedColors[ i ][3] = ((storedColors[ i ][3] * (storedColors[ i ][4] - 1)) + (resultColor[3])) / storedColors[ i ][4];
//  Serial.println(""); Serial.print("Red after: "); Serial.print(storedColors[ i ][1]);
//  Serial.println("");
//
//}
//
//void updateStoredColorCount(int i){
//  storedColors[ i ][4] += 1;
//}

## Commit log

2022-06-16 Add files via upload
    Fritzing
    [beadsorter.fzz]
2023-02-28 Fix broken STL #2
    [UM2_Sequencer_tube_modified_tighter_Higher_Motor.stl]
